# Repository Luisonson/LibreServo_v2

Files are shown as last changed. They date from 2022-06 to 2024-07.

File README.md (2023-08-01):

# 
An Open source controller to convert any servo motor to the best smart servo.

This project was born as a necessity of mine to build a biped robot with intelligent servos to be able to “feel the muscles” to walk more human like. In the past we had OpenServo, and I think this project inherits something from it, but OpenServo died many years ago and it didn't reach my expectations anyway (power, communications...), and the commercial alternatives are way too expensive (Dynamixel, Herkulex, Lynxmotion...).

My goal with LibreServo is to make any standard servo the “smartest” one in the market. The "gold standard" nowadays is Robotis-Dynamixel, LibreServo should be better than that, that’s my goal at least.

A few characteristics of LibreServo:

    Compatible with standard servo motors (No need to change the bottom cover of them!)
    Voltage: From 4.5V up to 18V (Recommended: 5-14V)
    Communications: RS-485 half-duplex. Max Speed 9Mbps. Daisy chained. CRC-16
    Amp: Up to 16A continuous (WSD3069DN56) (Version >2.3)
    Micro-Controller: STM32F301k8 (cortex-M4@72MHz)
    Position sensor: Magnetic encoder, 16 bits of resolution! 360 degrees (AEAT-8800). Using the servo motor potentiometer will be possible to lower the cost but will lost precision and some characteristics.
    For the encoder I have designed 3D parts to substitute the potentiometer and used the same hole/space than the original.
    LibreServo will generate their own curves (sine ramps, trapezoidal ramps, hermitian curves...)
    Current sensor: +-15A ACS711
Communication Protocol: <a href="https://www.libreservo.com/en/articulo/libreservo-commands-part-one">LibreServo Commands</a><BR>


More info in <a href="https://www.libreservo.com/en">LibreServo</a>.

<p align="center">
<a href="http://creativecommons.org/licenses/by-sa/4.0/">cc-by-sa</a></p>

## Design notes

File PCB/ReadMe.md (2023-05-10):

Here are the files (.brd and .sch) of KiCad 7.6.0 from LibreServo.<BR>
  In the "old" folder are the previous versions of the schematics.<BR>
  In the "Gerbers" folder are the production files.
#


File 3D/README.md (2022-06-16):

To know the position of the servomotor axis, LibreServo uses the AEAT-8800 16-bit encoder. This encoder replaces the potentiometer that the servomotors have and with it we get much more precision and allows the servomotor to rotate 360 degrees.

To achieve this, LibreServo makes use of a tiny 10.2x11.2 mm PCB to which a 3D printed part of the same size and shape as the original potentiometer is attached. This 3D printed part consists of 3 small parts, a 4x7x2mm bearing and a small 6x2.5mm diametrically magnetized magnet. Only a glue point is needed to fix the magnet. The rest of the parts, bearing and PCB are designed to be snap-fitted and fixed.

With the first release of the LibreServo software, the 3D parts have also been updated. The .stl is uploaded to the Libreservo github in the 3D folder. <strong>The parts are designed to be printed with 0.1mm layers.</strong>

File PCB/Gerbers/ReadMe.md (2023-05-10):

# Gerber files to production
In the "old" folder are the old versions of LibreServo. Version 2.3.1 is the first final version.<BR>


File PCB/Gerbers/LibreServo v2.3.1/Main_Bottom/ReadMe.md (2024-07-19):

This is a special version ordered by a user and can only be produced in 6 layers.
#

<BR>

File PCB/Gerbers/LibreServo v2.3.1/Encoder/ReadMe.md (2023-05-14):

# 
<BR>
This directory contains the gerbers of the encoder AEAT-8800 PCB (6 Layers). <BR>
To get the 4 layer version, just edit the .zip and delete the .G2 and .G3 files.

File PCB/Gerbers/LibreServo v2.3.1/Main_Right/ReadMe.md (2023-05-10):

# 
<BR>
This directory contains the gerbers of the main PCB with only one of the connectors on the right (6 Layers). <BR>
To get the 4 layer version, just edit the .zip and delete the .G2 and .G3 files.

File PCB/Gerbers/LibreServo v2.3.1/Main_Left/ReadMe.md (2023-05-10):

# 
<BR>
This directory contains the gerbers of the main PCB with only one of the connectors on the left (6 Layers). <BR>
To get the 4 layer version, just edit the .zip and delete the .G2 and .G3 files.

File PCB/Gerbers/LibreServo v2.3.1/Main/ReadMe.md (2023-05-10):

# 
<BR>
This directory contains the gerbers of the main PCB (6 Layers). <BR>
To get the 4 layer version, just edit the .zip and delete the .G2 and .G3 files.

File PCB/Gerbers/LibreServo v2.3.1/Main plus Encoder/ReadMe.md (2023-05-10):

# 
<BR>
This directory contains the gerbers of the main PCB plus the encoder's PCB (6 Layers), that you can separate thanks to the "mouse bites". <BR>
To get the 4 layer version, just edit the .zip and delete the .G2 and .G3 files.

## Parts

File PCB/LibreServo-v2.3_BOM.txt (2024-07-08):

Partlist exported from LibreServo v2.3.1 at 08/07/2024 10:16 @ https://github.com/Luisonson/LibreServo_v2 @ https://www.libreservo.com/

Part  Value               Device              Package           Description                          
B1    700mA@600Ω@100MHz   PBY100505T-601Y-N   0402              340mΩ ±25% 600Ω@100MHz 0402 Ferrite Beads 700mA                                    
B2    2A@600Ω@100MHz      VPB160808T-601Y-N   0603              100mΩ ±25% 600Ω@100MHz 0603 Ferrite Beads 2A                                     
C1    4.7u                CM05X5R475M25AH     0402              25V 4.7uF X5R ±20% 0402 Multilayer Ceramic Capacitors MLCC                                     
C2    100n                CL05B104KB54PNC     0402              50V 100nF X7R ±10% 0402 Multilayer Ceramic Capacitors MLCC                                     
C3    100n                CL05B104KB54PNC     0402              50V 100nF X7R ±10% 0402 Multilayer Ceramic Capacitors MLCC
C4    1u                  CL05A105KA5NQNC     0402              25V 1uF X5R ±10% 0402 Multilayer Ceramic Capacitors MLCC
C5    100n                CL05B104KB54PNC     0402              50V 100nF X7R ±10% 0402 Multilayer Ceramic Capacitors MLCC
C6    100n                CL05B104KB54PNC     0402              50V 100nF X7R ±10% 0402 Multilayer Ceramic Capacitors MLCC
C7    10u                 CL10A106MA8NRNC     0603              25V 10uF X5R ±20% 0603 Multilayer Ceramic Capacitors MLCC
C8    22u                 CL31A226KAHNNNE     1206              25V 22uF X5R ±10% 1206 Multilayer Ceramic Capacitors MLCC
C9    1u                  CL05A105KA5NQNC     0402              25V 1uF X5R ±10% 0402 Multilayer Ceramic Capacitors MLCC
C10   1u                  CL05A105KA5NQNC     0402              25V 1uF X5R ±10% 0402 Multilayer Ceramic Capacitors MLCC
C11   100n                CL05B104KB54PNC     0402              50V 100nF X7R ±10% 0402 Multilayer Ceramic Capacitors MLCC
C12   1u                  CL05A105KA5NQNC     0402              25V 1uF X5R ±10% 0402 Multilayer Ceramic Capacitors MLCC
C13   1u                  CL05A105KA5NQNC     0402              25V 1uF X5R ±10% 0402 Multilayer Ceramic Capacitors MLCC
C14   100n                CL05B104KB54PNC     0402              50V 100nF X7R ±10% 0402 Multilayer Ceramic Capacitors MLCC
C15   1u                  CL05A105KA5NQNC     0402              25V 1uF X5R ±10% 0402 Multilayer Ceramic Capacitors MLCC
C16   10u                 CL10A106MA8NRNC     0603              25V 10uF X5R ±20% 0603 Multilayer Ceramic Capacitors MLCC
C17   10u                 CL10A106MA8NRNC     0603              25V 10uF X5R ±20% 0603 Multilayer Ceramic Capacitors MLCC
C18   100n                CL05B104KB54PNC     0402              50V 100nF X7R ±10% 0402 Multilayer Ceramic Capacitors MLCC
C19   100n                CL05B104KB54PNC     0402              50V 100nF X7R ±10% 0402 Multilayer Ceramic Capacitors MLCC
C20   10n                 CL05B103KB5NNNC     0402              50V 10nF X7R ±10% 0402 Multilayer Ceramic Capacitors MLCC
C21   10n                 CL05B103KB5NNNC     0402              50V 10nF X7R ±10% 0402 Multilayer Ceramic Capacitors MLCC
C22   220uF               ERS1EM221E11OT      E2,5-6_MIN        220uF 25V 220mΩ@100kHz ±20% 340mA@100kHz Plugin,D6.3xL11mm Aluminum Electrolytic Capacitors - Leaded
C23   10u                 CL10A106MA8NRNC     0603              25V 10uF X5R ±20% 0603 Multilayer Ceramic Capacitors MLCC
C24   10u                 CL10A106MA8NRNC     0603              25V 10uF X5R ±20% 0603 Multilayer Ceramic Capacitors MLCC
M1    P5103EMA            P5103EMA            SOT23             P Channel 30V 3.8A 1W 85mΩ@4.5V,3.5A SOT-23(TO-236)                                     
M2    MOSFET_N+P          WSD3069DN56         DFN5X6            30V 16A 15mΩ@10V,10A 1.5V@250uA 1PCSNChannel+1PCSPChannel DFN-8(5.2x5.5)
M3    MOSFET_N+P          WSD3069DN56         DFN5X6            30V 16A 15mΩ@10V,10A 1.5V@250uA 1PCSNChannel+1PCSPChannel DFN-8(5.2x5.5)
M4    FAN3227/4           FAN3227TMPX         MLP8              Low Side 2 MOSFET 3A 12ns 9ns 4.5V~18V 3A WDFN-8(3x3) Gate Drivers
M5    FAN3227/4           FAN3227TMPX         MLP8              Low Side 2 MOSFET 3A 12ns 9ns 4.5V~18V 3A WDFN-8(3x3) Gate Drivers
NTC   10K@3380K NTC       NTCG063JF103FTB     0402_MIN          10kΩ 310uA 100mW ±1% 3380K ±1% 0201 NTC Thermistors
R1    12.5K               0402WGF1252TCE      0402              62.5mW Thick Film Resistors 50V ±100ppm/ºC ±1% 12.5kΩ 0402
R2    47K                 0402WGF4702TCE      0402              62.5mW Thick Film Resistors 50V ±100ppm/ºC ±1% 47kΩ 0402
R3    150K                0402WGF1503TCE      0402              62.5mW Thick Film Resistors 50V ±100ppm/ºC ±1% 150kΩ 0402
R4    10K                 0402WGF1002TCE      0402              62.5mW 10kΩ 50V Thick Film Resistors ±1% ±100ppm/ºC 0402
R5    51K                 TR0402B51K0Q1050Z   0402              63mW Thin Film Resistor 25V ±50ppm/ºC ±0.1% 51kΩ 0402
R6    187                 RC0402FR-07187RL    0402              62.5mW Thick Film Resistors 50V ±100ppm/ºC ±1% 187Ω 0402
R7    270                 0402WGF2700TCE      0402              62.5mW Thick Film Resistors 50V ±100ppm/ºC ±1% 270Ω 0402
R8    309                 CQ02WGF3090TCE      0402              62.5mW 50V ±100ppm/ºC ±1% 309Ω 0402
R9    10K                 0402WGF1002TCE      0402              62.5mW 10kΩ 50V Thick Film Resistors ±1% ±100ppm/ºC 0402
R10   1.1k                0402WGF1101TCE      0402              62.5mW Thick Film Resistors 50V ±100ppm/ºC ±1% 1.1kΩ 0402
R11   10K                 0402WGF1002TCE      0402              62.5mW 10kΩ 50V Thick Film Resistors ±1% ±100ppm/ºC 0402
R12   10K                 0402WGF1002TCE      0402              62.5mW 10kΩ 50V Thick Film Resistors ±1% ±100ppm/ºC 0402
R13   6                   WR04W6R04FTL        0402              62.5mW Thick Film Resistors 50V -200ppm/ºC 400ppm/ºC ±1% 6.04Ω 0402
R14   6                   WR04W6R04FTL        0402              62.5mW Thick Film Resistors 50V -200ppm/ºC 400ppm/ºC ±1% 6.04Ω 0402
R15   6                   WR04W6R04FTL        0402              62.5mW Thick Film Resistors 50V -200ppm/ºC 400ppm/ºC ±1% 6.04Ω 0402
R16   6                   WR04W6R04FTL        0402              62.5mW Thick Film Resistors 50V -200ppm/ºC 400ppm/ºC ±1% 6.04Ω 0402
R17   10K                 0402WGF1002TCE      0402              62.5mW 10kΩ 50V Thick Film Resistors ±1% ±100ppm/ºC 0402
R18   10K                 0402WGF1002TCE      0402              62.5mW 10kΩ 50V Thick Film Resistors ±1% ±100ppm/ºC 0402
R19   10K                 0402WGF1002TCE      0402              62.5mW 10kΩ 50V Thick Film Resistors ±1% ±100ppm/ºC 0402
R20   10K                 0402WGF1002TCE      0402              62.5mW 10kΩ 50V Thick Film Resistors ±1% ±100ppm/ºC 0402
RGB   LED_RGB_PLCC4_2.2X2 ASMB-KTF0-0A306     PLCC-4_2.2X2      SMD-4P,2x2.2mm Light Emitting Diodes (LED RGB)                                          
U$3   FFC-5               THD0510-05CL-GF     FFC-5-0.5         Clamshell 5P Bottom Contact Surface Mount，Right Angle 0.5mm SMD,P=0.5mm,Surface Mount，Right Angle FFC/FPC
U$4   FFC-5               THD0510-05CL-GF     FFC-5-0.5         Clamshell 5P Bottom Contact Surface Mount，Right Angle 0.5mm SMD,P=0.5mm,Surface Mount，Right Angle FFC/FPC
U$8   JST_PH-4_HOLEB      PH-4A               JST_PH-4_HOLE_B   1x4P 4P PH 1 2mm 4 Plugin,P=2mm Wire To Board Connector
U$9   JST_PH-4_HOLEB      PH-4A               JST_PH-4_HOLE_B   1x4P 4P PH 1 2mm 4 Plugin,P=2mm Wire To Board Connector
U$100 OSCILATOR@8MHz      SX1M8.000M10F30TNN  OSC-2X1.6         1.62V~3.63V ±10ppm 10mA ±30ppm CMOS 8MHz SMD2016-4P Oscillators
U1    STM32F301/2         STM32F301K8U6       QFN32             64KB 2V~3.6V ARM-M4 16KB 72MHz FLASH 24 UFQFPN-32(5x5) Microcontrollers
U2    MPM3610             MPM3610AGQV         MPM36XX           QFN-20(3x5) DC-DC Power Modules
U3    AP2112              AP2112K-3.3TRG1     SOT25             65dB@(100Hz,1kHz) 600mA Fixed 3.3V Positive electrode 6V SOT-25-5 Voltage Regulators - Linear, Low Drop Out (LDO) Regulators
U4    ACS711              ACS711KEXLT-15AB-T  ACS711-QFN        ±15.5A QFN-12(3x3) Current Sensors
U5    SIT3485             SIT3485EUA          MSOP-8            transceiver 12Mbps 1/1 MSOP-8 RS-485/RS-422 ICs
U10   AEAT-8800           AEAT-8800-Q24       QFN24             Encoders Prog 16Bits IC Magnetic Encoder

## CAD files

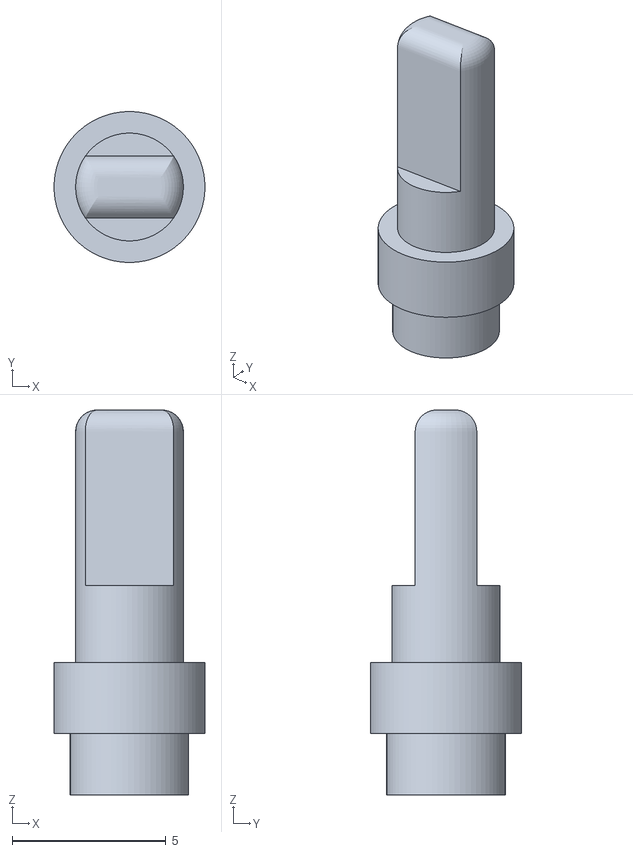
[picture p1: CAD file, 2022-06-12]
3D/LS_shaft_a.stl
4.90 x 4.90 x 12.5

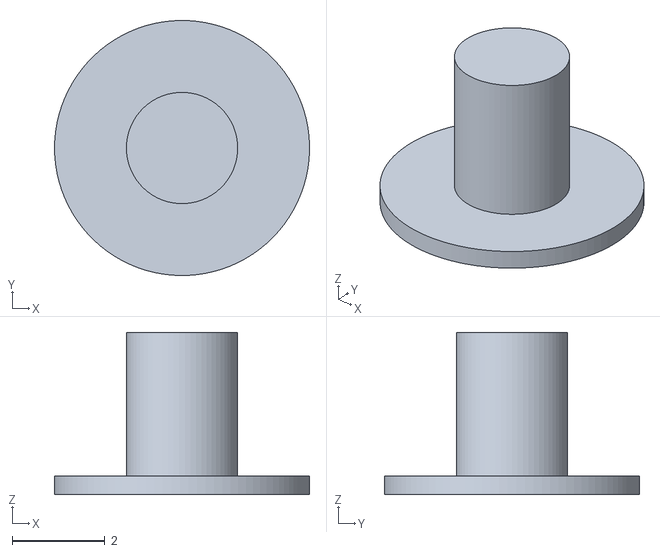
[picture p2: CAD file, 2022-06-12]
3D/LS_shaft_b.stl
5.50 x 5.50 x 3.50

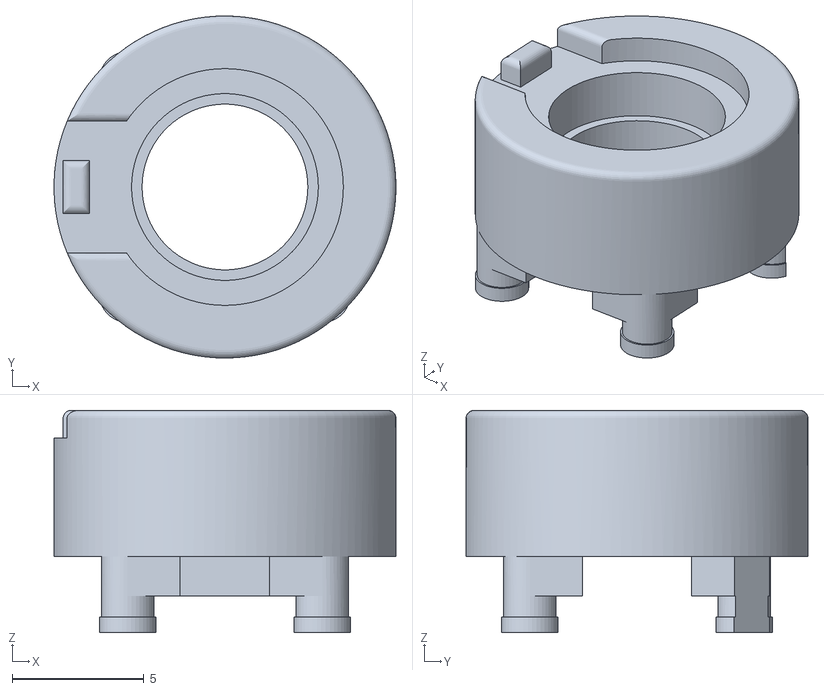
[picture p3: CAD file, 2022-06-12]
3D/LS_body.stl
13.0 x 13.0 x 8.45

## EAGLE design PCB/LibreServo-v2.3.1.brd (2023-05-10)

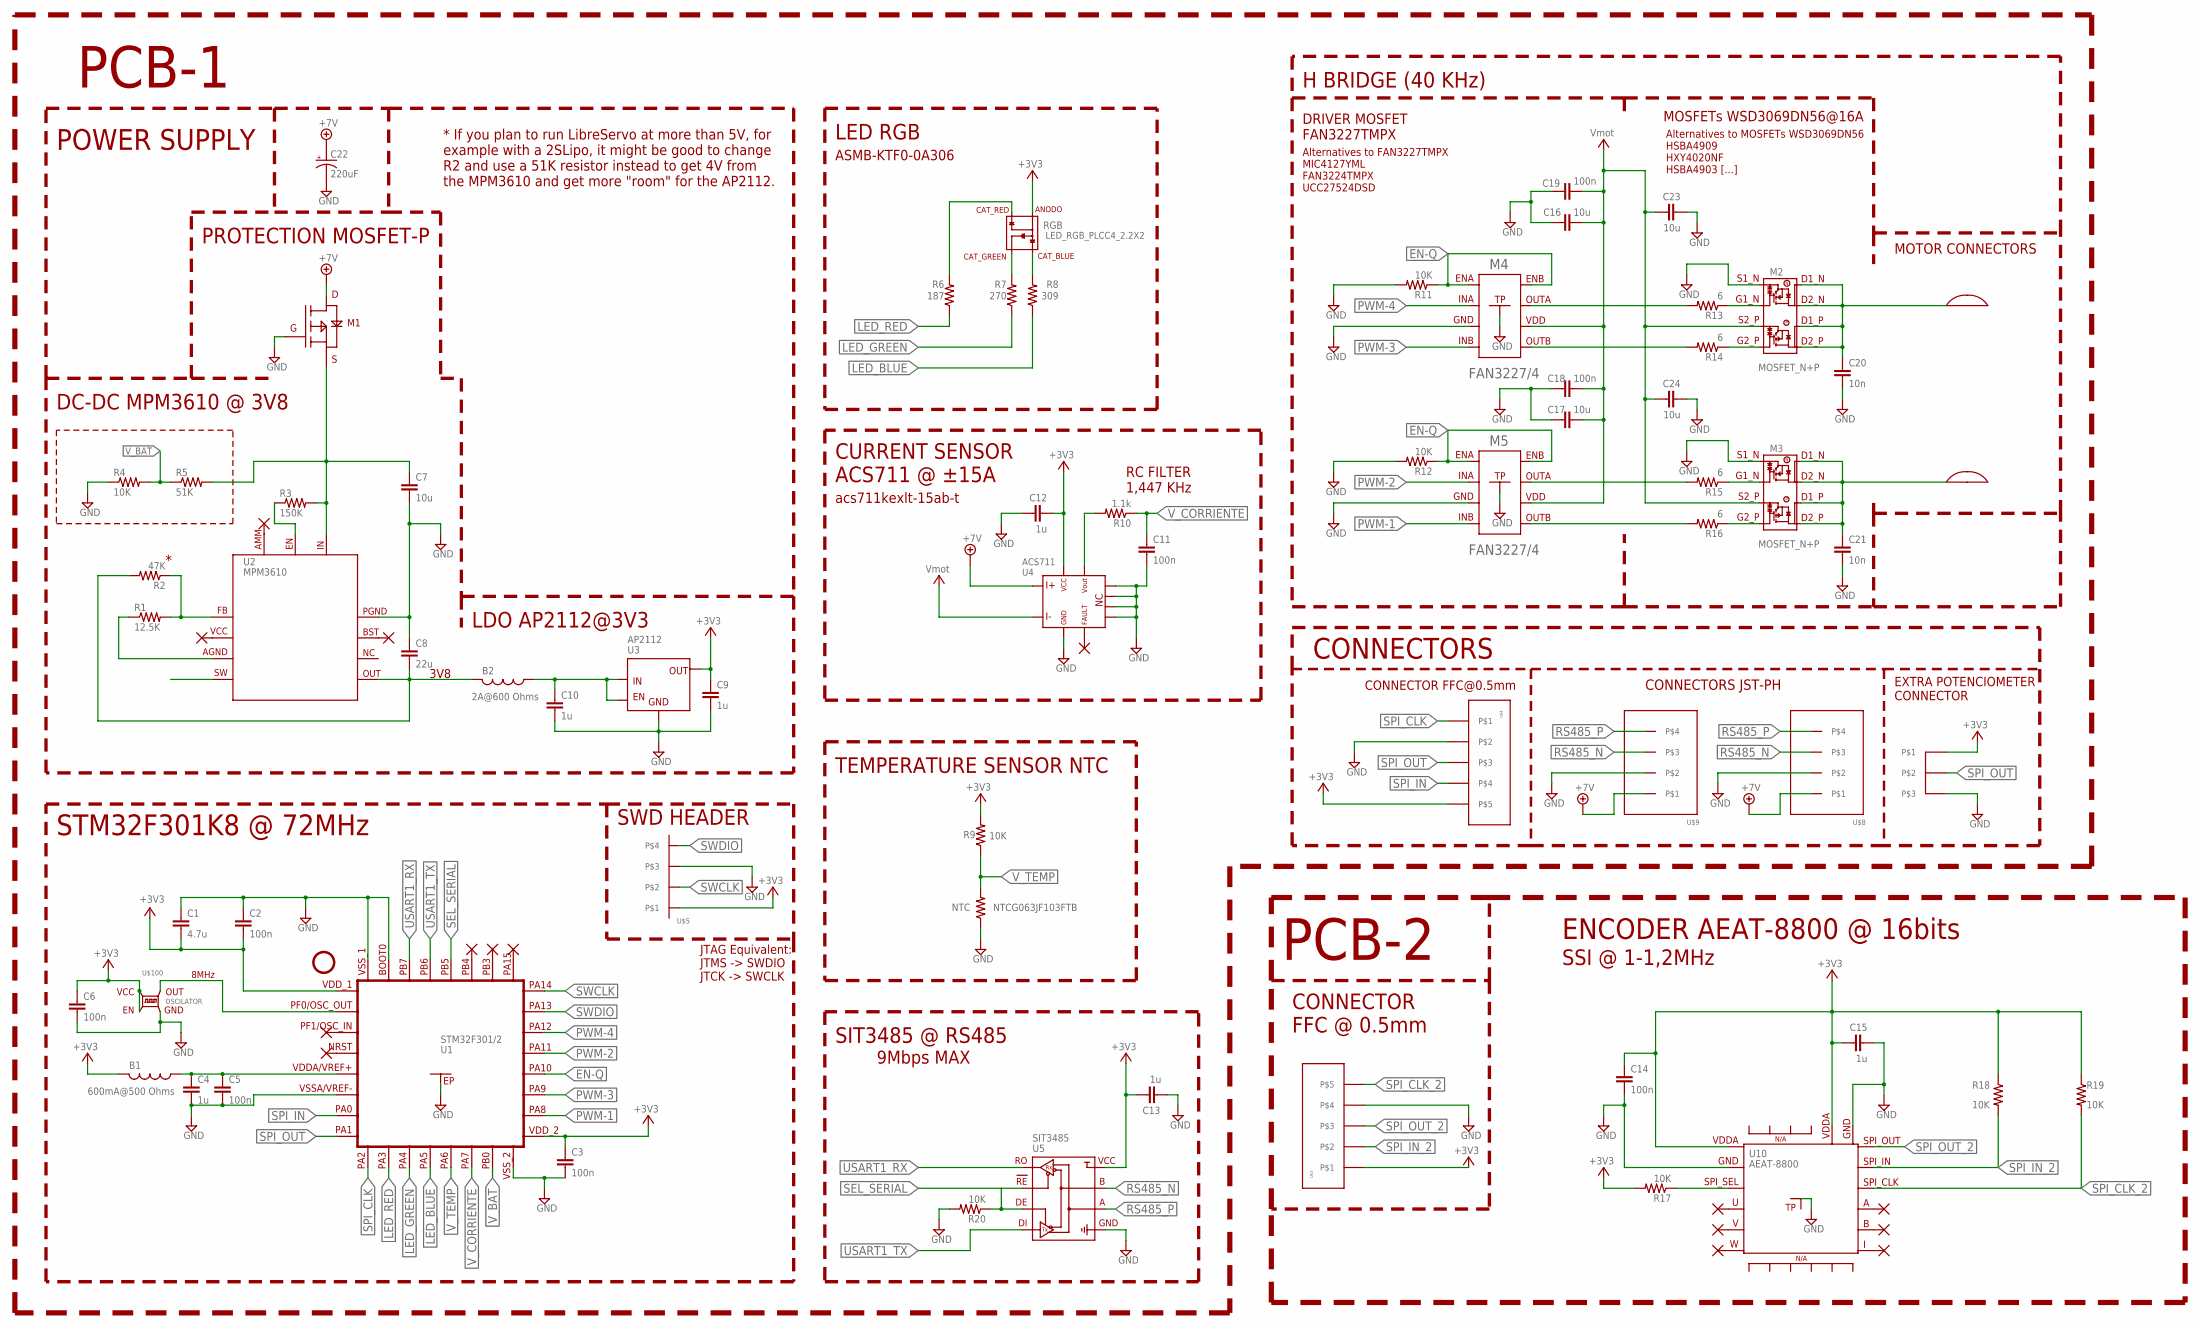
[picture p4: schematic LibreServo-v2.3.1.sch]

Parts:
B1: FERRITE_BEAD_0402; 0402
B2: FERRITE_BEAD_0603; 0603
C1: 4.7u; 0402
C2, C3, C5, C6, C11, C14, C18, C19: 100n; 0402
C4, C9, C10, C12, C13, C15: 1u; 0402
C7, C16, C17, C23, C24: 10u; 0603
C8: 22u; 1206
C20, C21: 10n; 0402
C22: 220uF; E2,5-6_MIN
M1: M1; SOT23
M2, M3: MOSFET_N+P; DFN5X6
M4, M5: FAN3227/4; MLP8
NTC: R-US0402_MIN; 0402_MIN
R1: 12.5K; 0402
R2: 47K; 0402
R3: 150K; 0402
R4, R9, R11, R12, R17, R18, R19, R20: 10K; 0402
R5: 51K; 0402
R6: 187; 0402
R7: 270; 0402
R8: 309; 0402
R10: 1.1k; 0402
R13, R14, R15, R16: 6; 0402
RGB: LED_RGB_PLCC4_2.2X2; PLCC-4_2.2X2
U1: STM32F301/2; QFN32
U2: MPM3610; MPM36XX
U3: AP2112; SOT25
U4: ACS711; ACS711-QFN
U5: SIT3485; MSOP-8
U10: AEAT-8800; QFN24
U$1, U$2: SLOT; SERVO_SLOT
U$3, U$4: FFC-5; FFC-5-0.5
U$5: HEADER_4_1.27_0.3
U$6: POTEN_SERVO
U$8, U$9: JST_PH-4_HOLEB; JST_PH-4_HOLE_B
U$100: OSCILATOR; OSC-2X1.6

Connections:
711_OUT: R10.2, U4.P$11
+3V3: B1.2, C1.2, C2.2, C3.1, C6.1, C9.1, C12.2, C13.2, R9.2, RGB.P$1 (ANODO), U1.1 (VDD_1), U1.17 (VDD_2), U3.5, U4.P$12, U5.P$8, U$4.P$5, U$5.P$1, U$6.P$1, U$100.P$1 (EN), U$100.P$4 (VCC)
+3V3_2: C14.1, C15.1, R17.2, R18.1, R19.1, U10.P$14, U10.P$19, U$3.P$1
+7V: C22.+, M1.P$2 (D), U4.P$1, U$8.P$1, U$9.P$1
CLK-8MHZ: U1.2 (PF0/OSC_IN), U$100.P$3 (OUT)
EN-Q: M4.P$1 (ENA), M4.P$8 (ENB), M5.P$1 (ENA), M5.P$8 (ENB), R11.1, R12.1, U1.20 (PA10)
GND: C1.1, C2.1, C3.2, C4.2, C5.2, C6.2, C7.2, C8.1, C9.2, C10.2, C11.2, C12.1, C13.1, C16.1, C17.1, C18.1, C19.1, C20.2, C21.2, C22.-, C23.2, C24.2, M1.P$1 (G), M2.P$1 (S1_N), M3.P$1 (S1_N), M4.P$3 (GND), M4.P$9 (TP), M5.P$3 (GND), M5.P$9 (TP), NTC.1, R4.1, R11.2, R12.2, R20.2, U1.6 (VSSA/VREF-), U1.16 (VSS_2), U1.31 (BOOT0), U1.32 (VSS_1), U1.EP, U2.P$12 (P$8_PGND), U2.P$13 (P$8_PGND), U2.P$14 (P$8_PGND), U3.2, U4.P$5, U4.P$7, U4.P$8, U4.P$9, U4.P$10, U5.P$5, U$4.P$2, U$5.P$3, U$6.P$3, U$8.P$2, U$9.P$2, U$100.P$2 (GND)
GND_2: C14.2, C15.2, U10.P$13, U10.P$20, U10.P$25, U$3.P$4
IN_AP2112: B2.1, C10.1, U3.1, U3.3
LED_BLUE: R8.1, U1.12 (PA5)
LED_GREEN: R7.1, U1.11 (PA4)
LED_RED: R6.1, U1.10 (PA3)
M1-OUT: C7.1, M1.P$3 (S), R3.2, R5.2, U2.P$16 (P$9_IN)
M2-OUT: C20.1, M2.P$5 (D2_P), M2.P$6 (D1_P), M2.P$7 (D2_N), M2.P$8 (D1_N), M2.P$9 (D1_N), U$1.P$1
M3-OUT: C21.1, M3.P$5 (D2_P), M3.P$6 (D1_P), M3.P$7 (D2_N), M3.P$8 (D1_N), M3.P$9 (D1_N), U$2.P$1
M4-OUTA: M4.P$7 (OUTA), R13.2
M4-OUTA-IN: M2.P$2 (G1_N), R13.1
M4-OUTB: M4.P$5 (OUTB), R14.2
M4-OUTB-IN: M2.P$4 (G2_P), R14.1
M5-OUTA: M5.P$7 (OUTA), R15.2
M5-OUTA-IN: M3.P$2 (G1_N), R15.1
M5-OUTB: M5.P$5 (OUTB), R16.2
M5-OUTB-IN: M3.P$4 (G2_P), R16.1
MPM3610_AGND: R1.1, U2.P$3 (P$3_AGND)
MPM3610_EN: R3.1, U2.P$17 (P$10_EN)
MPM3610_FB: R1.2, R2.1, U2.P$1 (P$1_FB)
MPM3610_SW: U2.P$4 (P$4_SW), U2.P$5 (P$4_SW), U2.P$6 (P$4_SW)
unnamed: R6.2, RGB.P$4 (CAT_RED)
unnamed: R7.2, RGB.P$3 (CAT_GREEN)
unnamed: R8.2, RGB.P$2 (CAT_BLUE)
unnamed: R17.1, U10.P$21
OUT_MPM3610: B2.2, C8.2, R2.2, U2.P$7 (P$5_OUT), U2.P$8 (P$5_OUT), U2.P$9 (P$5_OUT)
PWM-1: M5.P$4 (INB), U1.18 (PA8)
PWM-2: M5.P$2 (INA), U1.21 (PA11)
PWM-3: M4.P$4 (INB), U1.19 (PA9)
PWM-4: M4.P$2 (INA), U1.22 (PA12)
RS485_N: U5.P$7, U$8.P$3, U$9.P$3
RS485_P: U5.P$6, U$8.P$4, U$9.P$4
SEL_SERIAL: R20.1, U1.28 (PB5), U5.P$2, U5.P$3
SPI_CLK: U1.9 (PA2), U$4.P$1
SPI_CLK_2: R19.2, U10.P$10, U$3.P$5
SPI_IN: U1.7 (PA0), U$4.P$4
SPI_IN_2: R18.2, U10.P$11, U$3.P$2
SPI_OUT: U1.8 (PA1), U$4.P$3, U$6.P$2
SPI_OUT_2: U10.P$12, U$3.P$3
SWCLK: U1.24 (PA14), U$5.P$2
SWDIO: U1.23 (PA13), U$5.P$4
USART1_RX: U1.30 (PB7), U5.P$1
USART1_TX: U1.29 (PB6), U5.P$4
VDDA-FILTRADO: B1.1, C4.1, C5.1, U1.5 (VDDA/VREF+)
VMOT: C16.2, C17.2, C18.2, C19.2, C23.1, C24.1, M2.P$3 (S2_P), M3.P$3 (S2_P), M4.P$6 (VDD), M5.P$6 (VDD), U4.P$3
V_BAT: R4.2, R5.1, U1.15 (PB0)
V_CORRIENTE: C11.1, R10.1, U1.14 (PA7)
V_TEMP: NTC.2, R9.1, U1.13 (PA6)

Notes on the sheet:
SWD HEADER
STM32F301K8 @ 72MHz
POWER SUPPLY
PROTECTION MOSFET-P
DC-DC MPM3610 @ 3V8
LDO AP2112@3V3
LED RGB
ASMB-KTF0-0A306
CURRENT SENSOR ACS711 @ ±15A
RC FILTER 1,447 KHz
TEMPERATURE SENSOR NTC
SIT3485 @ RS485
H BRIDGE (40 KHz)
DRIVER MOSFET FAN3227TMPX
MOSFETs WSD3069DN56@16A
MOTOR CONNECTORS
PCB-2
ENCODER AEAT-8800 @ 16bits
CONNECTOR FFC @ 0.5mm
CONNECTORS
CONNECTOR FFC@0.5mm
CONNECTORS JST-PH
EXTRA POTENCIOMETER CONNECTOR
PCB-1
acs711kexlt-15ab-t
3V8
2A@600 Ohms
600mA@500 Ohms
NTCG063JF103FTB
SSI @ 1-1,2MHz
9Mbps MAX
8MHz
* If you plan to run LibreServo at more than 5V, for example with a 2SLipo, it might be good to change R2 and use a 51K resistor instead to get 4V from the MPM3610 and get more "room" for the AP2112.
Alternatives to FAN3227TMPX MIC4127YML FAN3224TMPX UCC27524DSD
Alternatives to MOSFETs WSD3069DN56 HSBA4909 HXY4020NF HSBA4903 [...]
JTAG Equivalent: JTMS -> SWDIO JTCK -> SWCLK

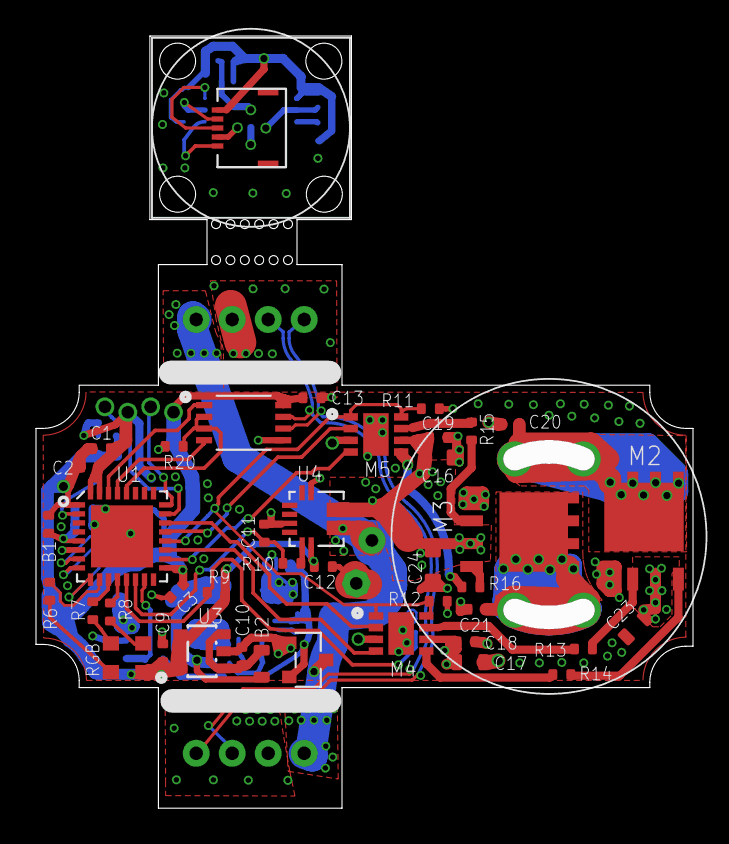
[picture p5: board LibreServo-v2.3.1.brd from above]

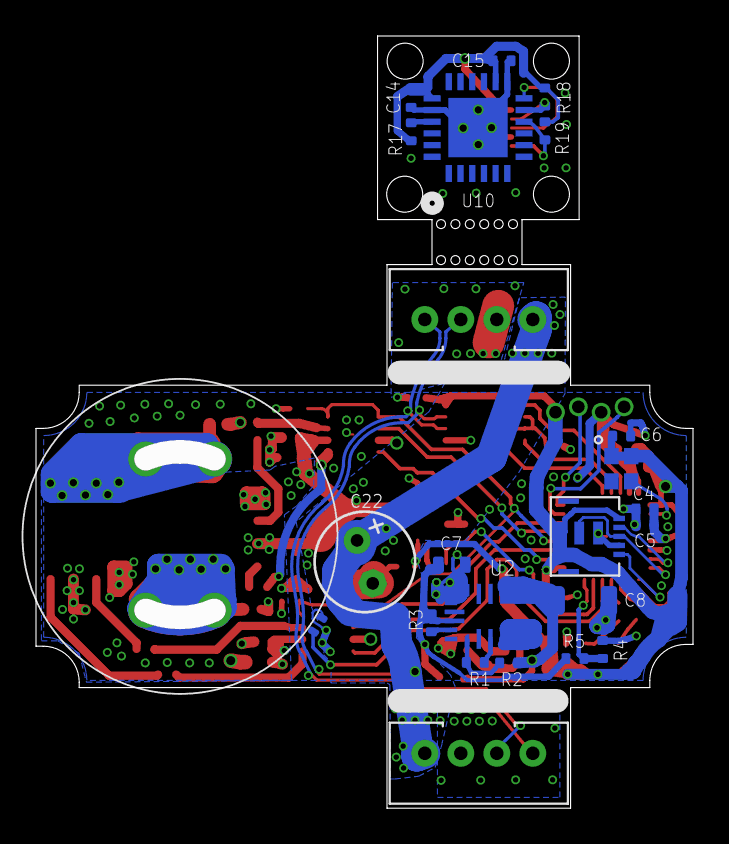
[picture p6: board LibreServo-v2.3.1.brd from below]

Board: 6 copper layers, 36.5 x 42.9 mm, 68 parts (23 on the bottom side), 54 nets.

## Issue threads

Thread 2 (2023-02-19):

LibreServo is neither Open Source nor Libre

abetusk, 2023-02-19:
As of this writing, the description for the LibreServo_v2 GitHub repository description states:

> An Open source controller to convert any servo motor to the best smart servo.

Yet the license in the [README.md](https://github.com/Luisonson/LibreServo_v2/blob/master/README.md) and source files are under a non-commercial Creative Commons license (the "NC" clause in the license).

The "non-commercial" clause makes this project not open source, in the common usage of the term "open source", and makes the project non-libre, in the common usage of the term libre as it relates to "[free software](https://en.wikipedia.org/wiki/Free_software)".

"Open Source" has a generally accepted meaning of being able to use the digital artifacts for commercial purposes. The [OSI](https://opensource.org/osd/) and Wikipedia's entry on [open-source licensing](https://en.wikipedia.org/wiki/Open-source_license) both articulate that commercial re-use is a (generally accepted) requirement of an "open source" license.

Further, the term "Libre" is, in my experience, usually used to further differentiate licensing terms. I use "Libre" to specifically indicate the "freedom" aspect of it, with the term "Libre" specifically chosen to avoid confusion with the multiple meanings of English word "free" as in "gratis" (no cost) versus the intended usage of "free" as in "freedom". I also use "Libre" to additionally differentiate it from the confusion people have with associating "Open Source" as "source available" instead of the accepted usage of "software that respects freedom".

Wikipedia's entry on [free software](https://en.wikipedia.org/wiki/Free_software) has "libre software" as a synonym.

If the intent of the project is to create a libre/free/open source software and hardware server motor controller, could you change the licensing terms, both in the README.md and in the headers of the source files to reflect this intent? For example dropping the non-commercial clause would make this project open source and libre.

If the intent is to keep the non-commercial clause of the license, indications of the project being "open source" should be removed as should the "Libre" in the project name, as it is neither open source nor Libre.

Luisonson, 2023-02-19:
Hi Abe,
On the one hand I wanted to tell you that I am Spanish, and I use the word "libre" with more meaning than you give it. It had nothing to do with the project being open or not, it was really a mention to the OpenServo project and regardless of the license, the name is not going to be changed.
On the other hand, I have been checking the license and you were right. I have already corrected the license.
Thanks for your interest in the project and if you have any other request, feel free to ask.

Closed 2023-02-19.

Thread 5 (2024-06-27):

BOM file location for PCB fabrication

ImShomu, 2024-06-27:
Hi @Luisonson,

Thanks for the amassing work. Can you please share the BOM xls and the latest PCB file location?
I would like to fabricate and test it.
I think the latest PCB is here as of 2024
1. https://github.com/Luisonson/LibreServo_v2/blob/master/PCB/LibreServo-v2.3.1.brd
2. https://github.com/Luisonson/LibreServo_v2/blob/master/PCB/LibreServo-v2.3.1.sch

Best
Shomu

Luisonson, 2024-07-08:
Hello @ImShomu ,

I have uploaded the BOM file:
https://github.com/Luisonson/LibreServo_v2/blob/master/PCB/LibreServo-v2.3_BOM.txt

ImShomu, 2024-07-09:
@Luisonson, thank you so much for the work!

Can I consider this to be the final PCB upgrade and the rest will be firmware updates going on?
Also one quick note, I was getting some errors when I opened the PCB in KICad. The 3D view was not coming correctly and KiCad was complaining about lot of errors in PCB.

Luisonson, 2024-07-09:
Hello @ImShomu ,
Yes, it is the final version. There should not be any changes, hopefully 🤞🤞🤞
Unfortunately, Libreservo was made using a version of Eagle from 8 years ago and in those days, the 3D view didn't exist, so it's not there. If you want to make LibreServo, just upload the [Gerber](https://github.com/Luisonson/LibreServo_v2/tree/master/PCB/Gerbers/LibreServo%20v2.3.1) you want to JLCPCB (upload directly the .zip file you want).
Nowadays Eagle software sucks, so new PCBs, because I am working on new projects using the LibreServo standard like a new 2 DC smart motor controller, are made using Kicad.
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

Luisonson, 2024-07-09:
If you need help in making LibreServo in JLCPCB, I can create a small help article.

Shomu-Maersk, 2024-07-09:
@Luisonson, that will be a lifesaver.

Also can you please upload the BOM in .csv format?
I tried to order the PCB via JLCPCB with components insertion.  They asked for a component placement file along with BOM file.
If you can help with that would be awesome!!

Best Shomu

ImShomu, 2024-07-09:
Also can you please upload the BOM in .csv format?
I tried to order the PCB via JLCPCB with components insertion. They asked for a component placement file along with BOM file.
If you can help with that would be awesome!!
Best Shomu

Luisonson, 2024-07-10:
Hello @ImShomu ,

I have to say that I have never asked for a component placement in any of my projects...

Here is the bom in CSV format (it is the same but adding a ';' as column separator) 😉

[LibreServo-v2.3_BOM.csv](https://github.com/user-attachments/files/16162701/LibreServo-v2.3_BOM.csv)

Note that not all the parts are in LCSC, they don't have the LED, the current sensor neither the encoder.

If you have to make another file to JLCPCB or something special, I would like to hear from you so I can add it to the documentation, please 😄

Closed 2024-07-08.

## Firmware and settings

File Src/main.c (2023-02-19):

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
/* Includes ------------------------------------------------------------------*/
#include "main.h"


/* USER CODE BEGIN PV */

char dma_tx_buff[DMA_TX_BUFF_SIZE+12] = { 0 };			//Se da 12 extra para facilitar el código y nunca salirnos de memoria
char dma_rx_buff[DMA_RX_BUFF_SIZE] = { 0 };

int pos_buff_rx = 0;

volatile uint16_t dma_adc1_buff[TAM_DMA_ADC1_BUFF] = { 0 };

extern volatile uint8_t enviado_USART1;					//Inicializado en LS_funciones.c

volatile uint32_t data_SSI_IN_old = 20000;
volatile long data_SSI_IN_internal = 0;
volatile long data_SSI_IN_vuelta = 0;

//volatile int correccion_enc[257] = { };

uint32_t tiempo_ms = 0;

extern volatile uint32_t ticks;					//Inicializado en funciones.c

/********************************************************************************************************/
uint16_t version_LS = 8;
/********************************************************************************************************/

volatile uint16_t ID_SERVO;

uint32_t vel_serie;

extern volatile uint8_t bat_estado;						//Inicializado en LS_funciones.c Estado batería 0=Good, 1=LOW, 2=HIGH
extern volatile uint8_t temp_estado;					//Inicializado en LS_funciones.c Estado temperature 0=Good, 1=HIGH_external, 2=HIGH_internal, 3=HIGH_BOTH

volatile boolean status_tone = FALSE;
extern volatile uint8_t saludo_inicial;					//inicializado en LS_flash.h Saludo Inicial (0=False, 1=True)
volatile boolean estado_FD = FALSE;

uint16_t VarValue1/*, VarValue2, VarValue3*/;

/* Virtual address defined by the user: 0xFFFF value is prohibited */
uint16_t VirtAddVarTab[NB_OF_VAR] = {0x0001, 0x0002, 0x0003};
uint16_t VarDataTab[NB_OF_VAR] = {0, 0, 0};

boolean error_read_init_flash = FALSE;


/*********************************************************
 * [0] -> Temp_interna
 * [1] -> Temp_externa
 * [2] -> Temp_interna_raw
 * [3] -> Temp_interna_kalman
 * [4] -> Temp_externa_raw
 * [5] -> Temp_externa_kalman
 * [6] -> Voltage
 * [7] -> Voltage_raw
 * [8] -> Voltage_kalman
 * [9] -> Corriente
 * [10] -> Corriente_raw
 * [11] -> Corriente_kalman
 * [12] -> Encoder_raw
 * [13] -> Encoder_kalman
 * [14] -> Velocidad_enc
 * [15] -> Aceleración_enc
 * [16] -> Velocidad_sim
 * [17] -> Aceleración_sim
 * [18] -> Pos_objetivo
 * [19] -> Error
 * [20] -> DError
 * [21] -> PDTerm
 * [22] -> Iterm
 * [23] -> PWM
 * [24] -> output_LS
 *********************************************************/

/* USER CODE END PV */

void SystemClock_Config(void);
static void MX_GPIO_Init(void);
static void MX_DMA_Init(void);
static void MX_ADC1_Init(void);
static void MX_TIM1_Init(void);
static void MX_USART1_UART_Init(void);
static void MX_TIM17_Init(void);
static void MX_TIM15_Init(void);
static void MX_TIM16_Init(void);
static void MX_TIM2_Init(void);
static void MX_NVIC_Init(void);
/**
  * @brief  The application entry point.
  * @retval int
  */
int main(void)
{
  /* MCU Configuration--------------------------------------------------------*/

  /* Reset of all peripherals, Initializes the Flash interface and the Systick. */
  LL_APB2_GRP1_EnableClock(LL_APB2_GRP1_PERIPH_SYSCFG);
  LL_APB1_GRP1_EnableClock(LL_APB1_GRP1_PERIPH_PWR);

  /* System interrupt init*/
  NVIC_SetPriorityGrouping(NVIC_PRIORITYGROUP_3);

  /* SysTick_IRQn interrupt configuration */
  NVIC_SetPriority(SysTick_IRQn, NVIC_EncodePriority(NVIC_GetPriorityGrouping(),7, 1));

  /* USER CODE BEGIN Init */
  F_LED_RGB(0,0,0); //Inicializar LED
  
  init_variables();
  /* USER CODE END Init */

  /* Configure the system clock */
  SystemClock_Config();

  /* USER CODE BEGIN SysInit */
  SysTick_Config(72000);			//Para que interrumpa cada milisegundo (ms). ticks++ . Configura SysTick como la interrupción de prioriordad M�?S BAJA
  MX_GPIO_Init();					//Se inicializa unas pocas líneas abajo de nuevo... no pasa nada
  init_USART1_rx_as_INPUT();


  /* Unlock the Flash Program Erase controller */
  FLASH_Unlock();

  /* EEPROM Init */
  EE_Init();

  if(READ_PIN(GPIOB,LL_GPIO_PIN_7) == 0)		//Pin USART1_RX
  {
	  uint32_t tiempo_reset, tiempo_led;
	  int tiempo_flash_led;
	  boolean ciclo_led = FALSE;
	  tiempo_reset = ticks;
	  tiempo_led = ticks;

	  tiempo_flash_led = 600;

	  GPIOA->BRR=LED_GREEN;				//Clear_pin
	  GPIOA->BRR=LED_RED;				//Clear_pin
	  GPIOA->BRR=LED_BLUE;				//Clear_pin

	  while (READ_PIN(GPIOB,LL_GPIO_PIN_7) == 0 && (ticks - tiempo_reset) < 6000)		//Wait 6 secs to restore LibreServo
	  {
		  if((ticks - tiempo_led) > tiempo_flash_led)
		  {
			  tiempo_led = ticks;
			  FLIP_PIN(GPIOA,LED_GREEN);
			  FLIP_PIN(GPIOA,LED_RED);
			  FLIP_PIN(GPIOA,LED_BLUE);
			  if(ciclo_led == FALSE) ciclo_led = TRUE;
			  else
			  {
				  ciclo_led = FALSE;
				  tiempo_flash_led = tiempo_flash_led / 1.3;
			  }
		  }
	  }
	  if ((ticks - tiempo_reset) >= 6000)
	  {
		  reset_flash();
	  }
  }

  if(EE_ReadVariable(0x0001,&VarValue1) == 1) 	//No se encuentra la variable
  {
	  EE_WriteVariable(0x0001,version_LS);
	  /*Escribir todas las variables*/
	  write_init_flash();
  }
  else if (VarValue1 != version_LS)
  {
	  EE_WriteVariable(0x0001,version_LS);
  }
  /*Escribir variables nuevas si faltaran*/
  add_new_values_flash();
  if(read_init_flash() != 0) error_read_init_flash = TRUE;

  init_crcccitt_tab();			//Inicializa la tabla de CRC. Por defecto CRC-16/AUG-CCITT
  
  get_kalman_gains();

  /* USER CODE END SysInit */

  /* Initialize all configured peripherals */
  MX_GPIO_Init();
  MX_DMA_Init();
  MX_ADC1_Init();
  MX_TIM1_Init();
  MX_USART1_UART_Init();
  MX_TIM17_Init();
  MX_TIM15_Init();
  MX_TIM16_Init();
  MX_TIM2_Init();

  /* Initialize interrupts */
  MX_NVIC_Init();
  /* USER CODE BEGIN 2 */
  
  while(dma_adc1_buff[31] == 0) {/*Wait to fill dma_adc1_buff*/}

  LL_TIM_EnableCounter(TIM17);			//Timer17 starts running (TIM17->CR1.CEN)
  LL_TIM_EnableIT_UPDATE(TIM17);		//Enable the Update interrupt in TIM17 (TIM17->DIER.UIE ---> TIM17->SR.UIF)
  LL_TIM_EnableCounter(TIM16);			//Timer16 starts running (TIM16->CR1.CEN)
  LL_TIM_EnableIT_UPDATE(TIM16);		//Enable the Update interrupt in TIM16 (TIM16->DIER.UIE ---> TIM16->SR.UIF)
  LL_TIM_EnableCounter(TIM15);			//Timer15 starts running (TIM15->CR1.CEN)
  LL_TIM_EnableIT_UPDATE(TIM15);		//Enable the Update interrupt in TIM15 (TIM15->DIER.UIE ---> TIM15->SR.UIF)
  LL_TIM_EnableCounter(TIM2);			//Timer2 starts running (TIM2->CR1.CEN)
  LL_TIM_EnableIT_UPDATE(TIM2);			//Enable the Update interrupt in TIM2 (TIM2->DIER.UIE ---> TIM2->SR.UIF)

  SET_PIN(GPIOA,LL_GPIO_PIN_10);  		//Habilitar el fan3227
  Delay_ms(20);
  
  LL_TIM_CC_EnableChannel(TIM1, LL_TIM_CHANNEL_CH1); /* Enable output on channel */
  LL_TIM_CC_EnableChannel(TIM1, LL_TIM_CHANNEL_CH1N); /* Enable output on channel */
  LL_TIM_CC_EnableChannel(TIM1, LL_TIM_CHANNEL_CH2N); /* Enable output on channel */
  LL_TIM_CC_EnableChannel(TIM1, LL_TIM_CHANNEL_CH2); /* Enable output on channel */

  LL_TIM_EnableCounter(TIM1);

  LL_TIM_EnableAllOutputs(TIM1);

  LL_DMA_SetDataLength(DMA1, LL_DMA_CHANNEL_4, sizeof(dma_tx_buff));
  LL_USART_ClearFlag_TC(USART1);


  /* USER CODE END 2 */

  /* Infinite loop */
  /* USER CODE BEGIN WHILE */

  if(saludo_inicial)
  {
	  F_LED_RGB(255,0,0);
	  tone(2093, 5, 700);				//2093Hz(DO6, 50ms, 1000 de amplitud)
	  tiempo_ms=ticks;
	  while( ticks - tiempo_ms < 50 ){/*Espera 30ms*/}
	  F_LED_RGB(0,255,0);
	  tone(3136, 5, 700);				//3136Hz(SOL6, 50ms, 1000 de amplitud)
	  tiempo_ms=ticks;
	  while( ticks - tiempo_ms < 50 ){/*Espera 30ms*/}
	  F_LED_RGB(0,0,255);
	  tone(2637, 5, 700);				//2637Hz(MI6, 50ms, 1000 de amplitud)
	  tiempo_ms=ticks;
	  while( ticks - tiempo_ms < 50 ){/*Espera 30ms*/}
	  F_LED_RGB(255,255,255);
	  tone(4186, 15, 700);			//4186Hz(DO7, 100ms, 1800 de amplitud [máxima amplitud])
	  F_LED_RGB(0,0,0);
  }

  memset(dma_tx_buff,0,strlen(dma_tx_buff));			//fill dma_tx_buff with 0s
  if(error_read_init_flash)
  {
	dma_tx_buff[0] = 'F';
	dma_tx_buff[1] = 'L';
	dma_tx_buff[2] = 'A';
	dma_tx_buff[3] = 'S';
	dma_tx_buff[4] = 'H';
	dma_tx_buff[5] = ' ';
	dma_tx_buff[6] = 'E';
	dma_tx_buff[7] = 'R';
	dma_tx_buff[8] = 'R';
	dma_tx_buff[9] = 'O';
	dma_tx_buff[10] = 'R';
	dma_tx_buff[11] = 10;
	dma_tx_buff[12] = 13;
	enviado_USART1 = FALSE;
	LL_DMA_SetDataLength(DMA1, LL_DMA_CHANNEL_4, strlen(dma_tx_buff));
	GPIOB->BSRR=LL_GPIO_PIN_5;
	LL_DMA_EnableChannel(DMA1,LL_DMA_CHANNEL_4);
	while(1) {};											//Something went wrong...
  }

  ////data_SSI_IN_old = 0;

  while (1)			//main loop
  {
	  if(status_tone)
	  {
		  if(bat_estado == 0)
		  {
			  comando_tone();
			  status_tone = FALSE;
		  }
		  else status_tone = FALSE;
	  }
	  if(bat_estado == 1)		//BAT_LOW
	  {
		  tiempo_ms = ticks;

		  for(int temp_i = 255; temp_i >=0; temp_i = temp_i - 8)
		  {
			while( (ticks - tiempo_ms) < 15 ){/*Espera 15ms*/}
			tiempo_ms = ticks;
			F_LED_RGB(0,0,temp_i);
		  }
		  
		  F_LED_RGB(0,0,0);
		  tiempo_ms = ticks;
		  while( (ticks - tiempo_ms) < 1000 ){/*Espera 1000ms*/}

	  }
	  else if(bat_estado == 2)		//BAT_HIGH
	  {
		  tiempo_ms = ticks;

		  for(int temp_i = 255; temp_i >= 0; temp_i = temp_i - 8)
		  {
			while( (ticks - tiempo_ms) < 15 ){/*Espera 15ms*/}
			tiempo_ms = ticks;
			F_LED_RGB(temp_i,temp_i,0);
		  }
		  
		  F_LED_RGB(0,0,0);
		  tiempo_ms = ticks;
		  while( (ticks - tiempo_ms) < 1000 ){/*Espera 1000ms*/}

	  }
	  if ( temp_estado != 0 )		//ANY TEMPERATURE HIGH
	  {
		  tiempo_ms = ticks;

		  for(int temp_i = 255; temp_i >= 0; temp_i = temp_i - 8)
		  {
			while( (ticks - tiempo_ms) < 15 ){/*Espera 15ms*/}
			tiempo_ms = ticks;
			F_LED_RGB(temp_i,0,0);
		  }
		  
		  F_LED_RGB(0,0,0);
		  tiempo_ms = ticks;
		  while( (ticks - tiempo_ms) < 1000 ){/*Espera 1000ms*/}
	  }

	  if(estado_FD == TRUE)
	  {
		  if(bat_estado == 0)
		  {
			  comando_FD();
			  estado_FD = FALSE;
		  }
		  else estado_FD = FALSE;
	  }
    /* USER CODE END WHILE */

    /* USER CODE BEGIN 3 */
  }
  /* USER CODE END 3 */
}

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


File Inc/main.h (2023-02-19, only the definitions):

#define DMA_RX_BUFF_SIZE            12
#define SERIAL_BUFF_SIZE            100
#define DMA_TX_BUFF_SIZE            300
#define LS_TASK_SCHEDULER_SIZE		100
#define LS_TASK_SERIAL_SIZE			15
#define TAM_BUFF_SENSORES			26
#define TAM_DMA_ADC1_BUFF			32
#define degree_to_radian			0.0174533f
#define LED_GREEN LL_GPIO_PIN_4
#define LED_RED LL_GPIO_PIN_5
#define LED_BLUE LL_GPIO_PIN_3
#define LONG_MIN					-2147483647L // -(2^31 - 1)
#define NUM_VARIABLES				64
#define NVIC_PRIORITYGROUP_0         ((uint32_t)0x00000007) /*!< 0 bit  for pre-emption priority,
#define NVIC_PRIORITYGROUP_1         ((uint32_t)0x00000006) /*!< 1 bit  for pre-emption priority,
#define NVIC_PRIORITYGROUP_2         ((uint32_t)0x00000005) /*!< 2 bits for pre-emption priority,
#define NVIC_PRIORITYGROUP_3         ((uint32_t)0x00000004) /*!< 3 bits for pre-emption priority,
#define NVIC_PRIORITYGROUP_4         ((uint32_t)0x00000003) /*!< 4 bits for pre-emption priority,

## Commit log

2018-06-24 Test de git
    Test de git
2018-07-03 Add files via upload
    Prueba Interrupt TIM17
2018-07-04 Led with struct
2018-07-05 Uso de extern en variables...
2018-07-06 TIM17 Prescaler config fix
    [main.c]
2018-07-06 LEDs fix bugs
2018-07-06 LED testing
2018-07-09 Led Bug Fix And rainbow RGB
    [main.c]
2018-09-02 Añadido ficheros PCB
    [LibreServo_v1.brd, LibreServo_v1.sch, LibreServo_v1_a.brd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]
2018-10-10 LibreServo v1.c
    [LibreServo_v1.brd, LibreServo_v1.sch, LibreServo_v1_a.brd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]
2023-01-20 Add files via upload
    New version 2.1
    [LibreServo-v2.1.brd, LibreServo-v2.1.sch]
2023-05-10 Hardware Final version. v2.3.1
    [LibreServo-v2.3.1.brd, LibreServo-v2.3.1.sch]
2024-07-08 Added the BOM file
2024-07-18 Create One Connector Bottom folder

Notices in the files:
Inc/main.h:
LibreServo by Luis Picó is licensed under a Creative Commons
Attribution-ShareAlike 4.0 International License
